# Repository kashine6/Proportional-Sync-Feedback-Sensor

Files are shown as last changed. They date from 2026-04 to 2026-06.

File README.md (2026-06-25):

# PSF (Proportional Sync Feedback) Sensor for MMU

> **A kit made by the author is now available on AliExpress.**
>   
> [Vano3dla-Aliexpress](https://www.aliexpress.com/item/1005010470743517.html)
>
> **Authorized Resellers**
> * [DREMC](https://store.dremc.com.au/en-us/products/vano3dla-psf-sensor-kit-proportional-sync-feedback-sensor-for-mmu) (Australia)
> * [OneTwo3D](https://www.onetwo3d.co.uk/product/psf-proportional-sync-feedback-sensor-for-mmu/) (UK)
> 
> **Additional authorization information:**  
> Trianglelab and BLV are authorized to use the PSF Kit in their MMU kits.
>
> Contact me on Discord (Happy Hare): jacksky007  

This is a Mini Proportional Sync Feedback Sensor solution designed for MMU systems.  

**Note:**

1. After updating to V1.1,   
it should be possible to find a usable ADC interface and a suitable voltage interface on **all MMU boards**.
2. Currently shifted to the default **single-spring version**. It provides constant compression, which reduces the apparent load on the extruder stepper and helps overcome Bowden friction.
   The STLs folder still includes the dual-spring version, which has already been deprecated.
3. **HappyHare** provides strong support for PSF. [WIKI LINK](https://github.com/moggieuk/Happy-Hare/wiki/Synchronized-Gear-Extruder)  
Now HappyHare supports using the PSF as the extruder entry sensor for filament detection.[PULL](https://github.com/moggieuk/Happy-Hare/pull/936)
4. **AFC** currently does not support PSF.
5. This is a prototype design. You can use the PCB below to develop your own custom mods or designs, or even simply use a Hall sensor instead of the PCB.

**Other case versions:**

1. **Ningpj** designed a **More Stumpy version** for ERCF.  [LINK](https://github.com/ningpj/Stumpy_PSF_Sensor)
2. An version developed by **DW-Tas** for **EMU**.  [LINK](https://github.com/DW-Tas/EMU/tree/main/STL/Tension-compression-sensor/Proportional%20Sync%20Feedback%20(PSF)%20Version)
3. An version developed by **Batalhoti** for **quattro-box v2**.  [LINK](https://github.com/Batalhoti/QuattroBox/tree/main/QuattroBox_v2_Beta/STLs/hub_psf)

## 🧩 What Is a Proportional Sync Feedback Sensor?

The Proportional Feedback Sensor is a more advanced feedback solution that uses analog signals.

Unlike other solutions that rely on D2F switches, it:

- **Outputs a signal ranging from 0 to 1**
- **0.5 represents the neutral position**

With this signal, the printer can determine the exact current position of the feedback slider and adjust it toward neutral at any moment.

Happy-Hare has developed many powerful additional features for this type of sensor. 

For details, please refer to the relevant Happy-Hare documentation.

## 🛠 Hardware Design

This design does not use a dedicated standalone mainboard.
Instead, it leverages the ADC input already available on existing MMU boards.

If you want to produce the boards yourself, the **PCB Gerber files** are provided and can be used under the license.
If you prefer not to make the boards yourself, you can get the kit mentioned below.

Both the DRV5055A2 and MT9105ET Hall sensors can be used in my test.

**✅ PSF Board Schematic and PCB**

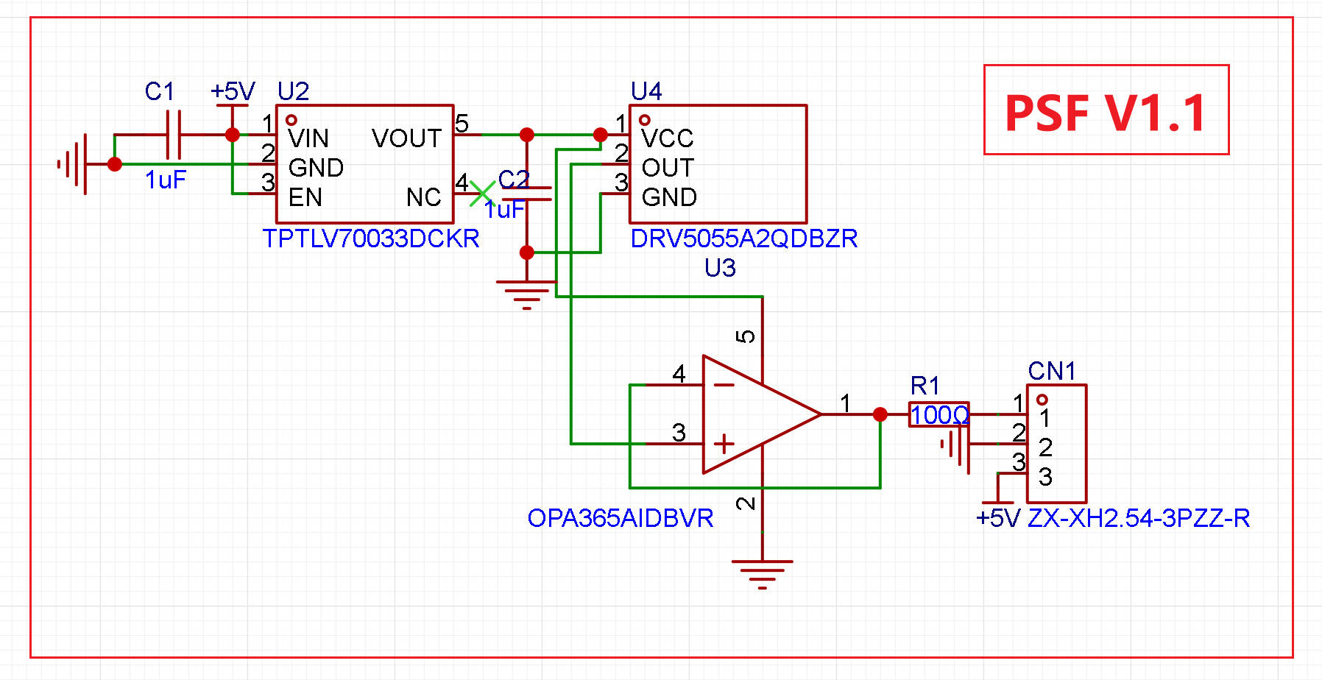
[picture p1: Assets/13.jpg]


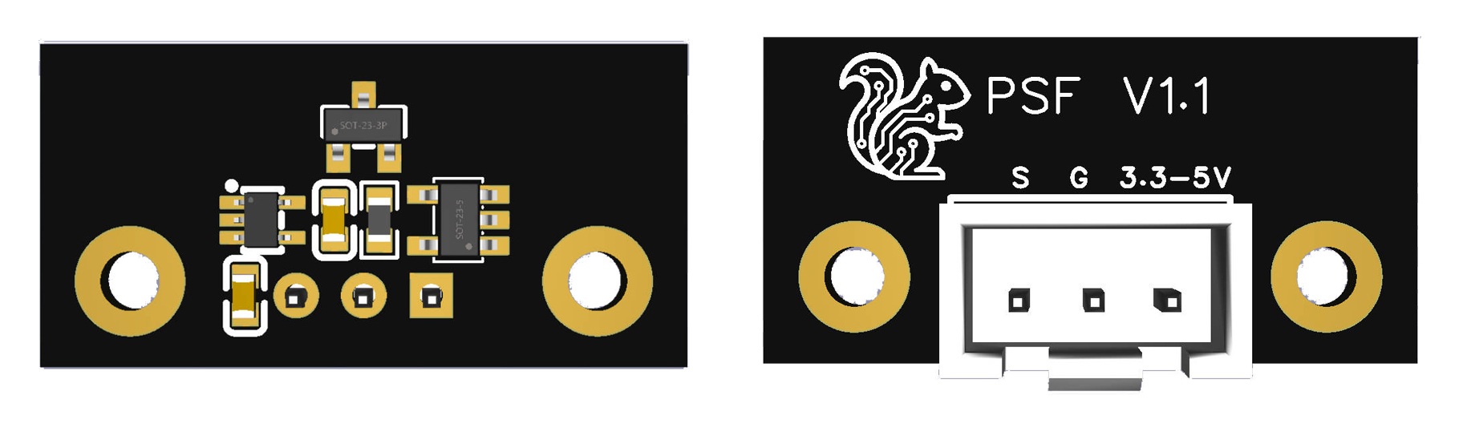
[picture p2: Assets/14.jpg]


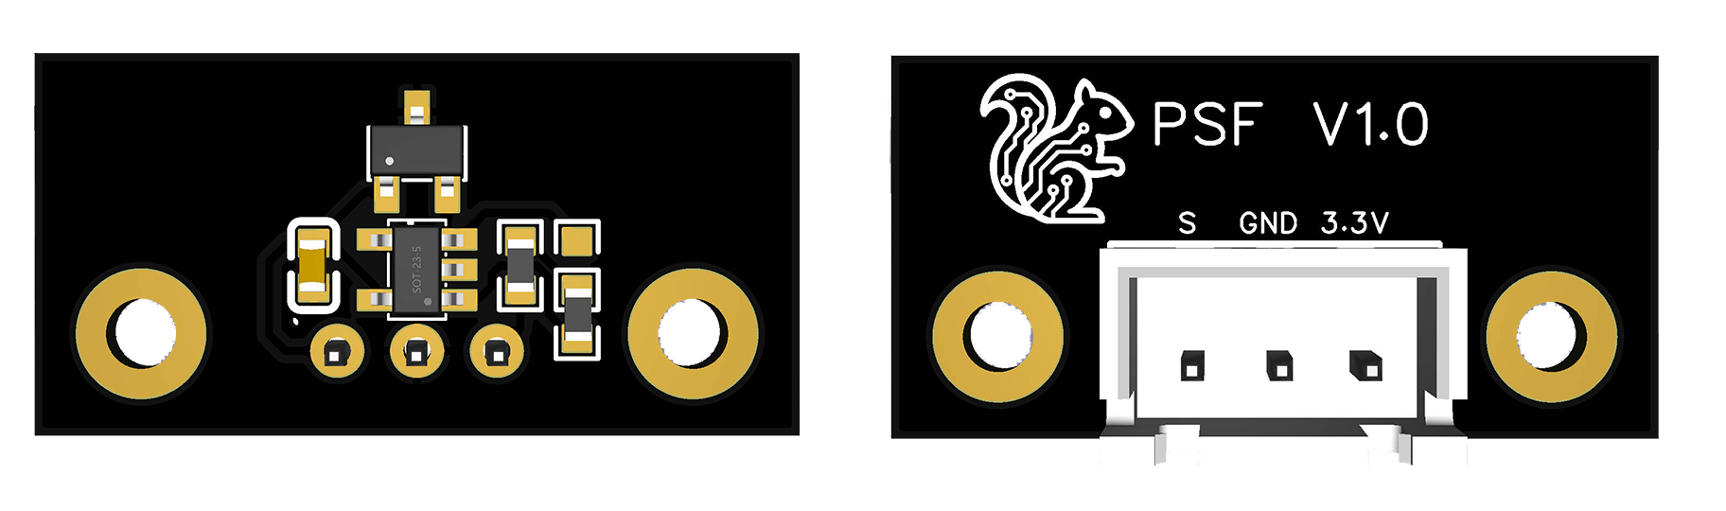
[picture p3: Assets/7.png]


**✅PCB Changelog**

V1.1
- Added wide input voltage support (3.3V–5V) compared to v1.0

V1.0
- Supports 3.3V input only
- Compatible with ADC interfaces with and without pull-up resistors

**✅Important Notice**

- You must connect the signal output to a pin that supports ADC input.

  > Recommended ADC Pins for common mainboards are shown in the diagram below.

- Version 1.1 supports a wide input voltage range of 3.3V–5V, while version 1.0 requires the power input to be 3.3V only.

  > ⚠️⚠️Do NOT use `5V` in Version 1.0 — this may damage your controller board.⚠️⚠️

**✅ADC Pull-up Considerations** 

Some boards—such as **MMB, EBB36, or EBB42**—have **built-in pull-up resistors** on all available ADC inputs.

To support both boards with and without pull-up resistors,  this sensor board uses a special design compatible with both cases.

Using an MMU board with ADC pull-ups will cause the sensor's ADC reading to shift upward (not constant; this has been minimized using the amplifier). 
You can adjust the neutral position value in the configuration to fix this issue.

## 📍 Recommended ADC GPIOs
You can refer to the chip datasheet to find all GPIOs that support ADC. Below, only one usable pin is marked.  

A list of recommended ADC-capable GPIOs for common MMU boards will be provided below:
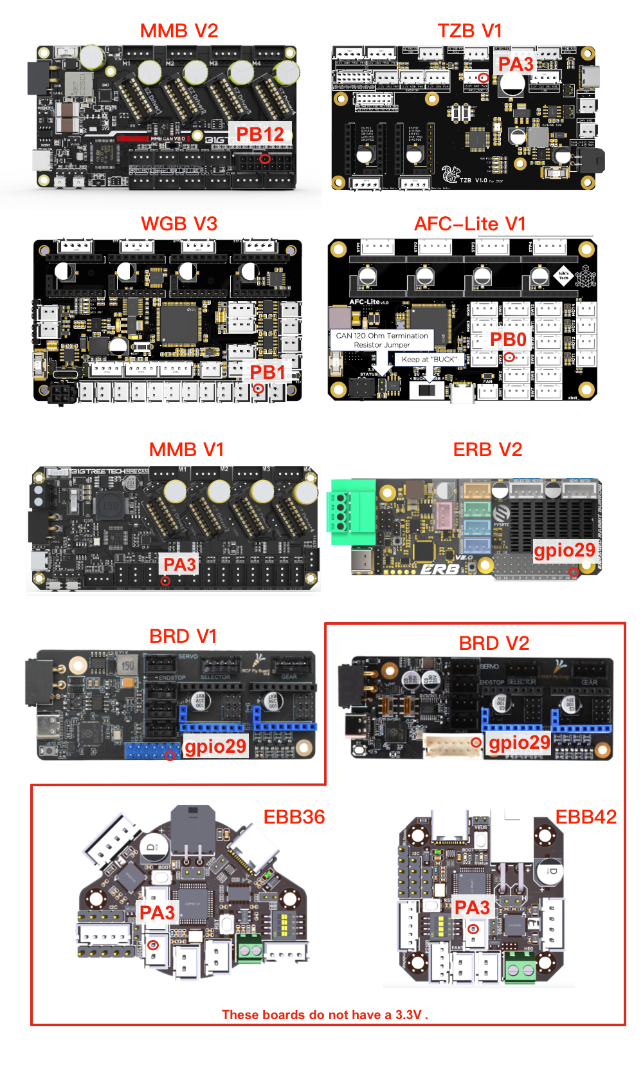
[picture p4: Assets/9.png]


## 📦 Bill of Materials (BOM)

| Item | Specification | Quantity |
| --- | --- | --- |
| **PSF Board** | — | 1 |
| **Spring** | 0.4 mm × 6 mm × 25 mm, spring steel | 1 |
| **Magnet** | D4 mm × 15 mm N35 | 1 |
| **ECAS04 Bowden connector** | — | 2 |
| **ECAS_Clip** | Please use the STL file for printing to ensure consistent thickness | 2 |
| **M2×6 mm SHCS screw** | | 4 |
| **5V-to-3.3V Step-Down Module** | Optional: Only required for V1.0 PCB if your board doesn’t provide a 3.3V. | 1 |

**A kit is available on AliExpress:**  

[Aliexpress](https://www.aliexpress.com/item/1005010470743517.html)

## 🔧 Configuration & Calibration

At the moment, `Happy-Hare` has **integrated** support for Proportional Feedback Sensors, and the relevant Wiki documentation has already been published. 

👉➡️:  [https://github.com/moggieuk/Happy-Hare/wiki/Synchronized-Gear-Extruder](https://github.com/moggieuk/Happy-Hare/wiki/Synchronized-Gear-Extruder) 

For more detailed configuration, please refer to the HappyHare Wiki.

For PSF Sensor one-Spring:  

```  
sync_feedback_buffer_range: 14.5		# Travel in "buffer" between compression/tension or one sensor and end (see above)
sync_feedback_buffer_maxrange: 14.5	    # Absolute maximum end-to-end travel (mm) provided by buffer (see above)  
```

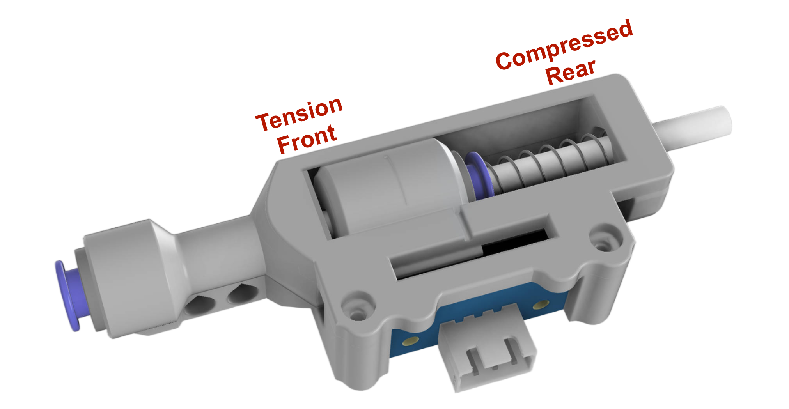
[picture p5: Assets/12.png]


#### ✅ PSF Automatic Calibration

Happy-Hare provides a calibration command, `MMU_CALIBRATE_PSENSOR`, to automatically calibrate the values of the three ADCs. 

Before running this command, you need to load the filament into the toolhead.

**Note:** If the extruder slips or repeated testing at the same position causes abnormal results, you can use manual calibration, which is simpler.

```
$ MMU_CALIBRATE_PSENSOR
...
// Calibration Results:
// As wired the recommended setting (in mmu_hardware.cfg) is:
// [mmu_sensors]
// sync_feedback_analog_max_compression: 0.0023
// sync_feedback_analog_max_tension:     0.9979
// sync_feedback_analog_neutral_point:   0.5001
// After updating, restart klipper
...
```
Please manually update the test results in the hardware.cfg file.

#### ✅ PSF Manual Calibration

Happy-Hare provides a command, `MMU_QUERY_PSENSOR`, to obtain the current raw ADC value. 

```
$ MMU_QUERY_PSENSOR
echo: PSENSOR Enabled: True  Value: -1.0  Raw Value: 0.997
```

You can remove the PSF PCB and place it in a magnetic-field-free environment, use this command to get the value of `sync_feedback_analog_neutral_point`. 

Then, move the slider to the Tension and Compression positions respectively to obtain the values of `sync_feedback_analog_max_tension` and `sync_feedback_analog_max_compression`.



## 🙏 References & Acknowledgements

- The CAD design is based on modifications of [Tshine's Filament Sync Sensor](https://makerworld.com/en/models/507573).  
- The Proportional Sync Feedback concept is inspired by [OpenAMS FPS](https://github.com/OpenAMSOrg/filament-buffer).  
- Thanks to moggieuk, igiannakas, ningpj and KnightRadiant for their excellent code contributions related to Proportional Sync Feedback.

## 😢 License

**This work is licensed under a**
[Creative Commons Attribution-NonCommercial-ShareAlike 4.0 International License][cc-by-nc-sa].

[][cc-by-nc-sa]

[cc-by-nc-sa]: http://creativecommons.org/licenses/by-nc-sa/4.0/
[cc-by-nc-sa-image]: https://licensebuttons.net/l/by-nc-sa/4.0/88x31.png
[cc-by-nc-sa-shield]: https://img.shields.io/badge/License-CC%20BY--NC--SA%204.0-lightgrey.svg

**License clarification regarding use (PCB only):**

- If you are an individual user, feel free to use it. You may choose to purchase a kit or manufacture the PCB yourself using the provided Gerber files.

- If you wish to sell PFS as a product, you must obtain a commercial license beforehand. 

- You may refer to this design for use in other applications, but proper attribution and authorization are required.

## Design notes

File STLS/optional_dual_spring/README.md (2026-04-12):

##  ⚙️ Calibration for dual_spring

**1. Enable detailed logging**

In `mmu_parameters.cfg`, temporarily set:

```
log_level: 4
```

This will let you observe the sensor state in real time.

You need to adjust the configuration in the `mmu_hardware.cfg` file within HappyHare according to the situation.

**2. Determine the correct direction (`sync_feedback_fps_reversed`)**

Move the slider to its left and right limit positions and observe the log output:

- If the front-end trigger reports `tension`, set:

  ```
  sync_feedback_fps_reversed: True
  ```

- If the front-end trigger reports **`compressed`**, set:

  ```
  sync_feedback_fps_reversed: False
  ```

**3. Set the neutral position (`sync_feedback_fps_set_point`)**

```
sync_feedback_fps_set_point: 0.5
```

Notes:

- On boards `without ADC pull-ups`, the idle value should be very close to **0.5**.
- On boards `with pull-ups`, a small offset is normal (typically **0.45–0.55**).
- You may adjust this value slightly depending on whether the neutral reading drifts toward 0 or toward the extremes.
- Whether the value rises or falls depends on the `magnet orientation.

**4. Adjust the usable range (`sync_feedback_fps_range_multiplier`)**

The Hall sensor is non-linear near its extremes, so the design does not use the full ADC range by default.

Increase this multiplier (e.g., **1.1 or 1.2**) so that the left/right extremes map closer to ±1 in the firmware logs.

Example log messages when correctly tuned:

```
STEPPER: MmuSyncFeedbackManager(inactive): Got sync force feedback update. State: tension (-1.0)
STEPPER: MmuSyncFeedbackManager(inactive): Got sync force feedback update. State: compressed (1.0)
```

Default value:

```
sync_feedback_fps_range_multiplier: 1.0
```

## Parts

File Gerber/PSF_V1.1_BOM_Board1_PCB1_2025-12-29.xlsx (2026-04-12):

No. | Quantity | Comment | Designator | Footprint | Value | Manufacturer Part | Manufacturer | Supplier Part | Supplier
1 | 2 | 1uF | C1,C2 | C0603 | 1uF | CGA0603X5R105K500JT | HRE(芯声) | C6119852 | LCSC
2 | 1 | 100Ω | R1 | R0603 | 100Ω | RC0603FR-07100RL | YAGEO(国巨) | C105588 | LCSC
3 | 1 | ZX-XH2.54-3PZZ-R | S G | CONN-TH_3P-P2.50_ZX-XH2.54-3PZZ-R |  | ZX-XH2.54-3PZZ-R | Megastar(兆星) | C22388625 | LCSC
4 | 1 | TPTLV70033DCKR | U2 | SC-70-5_L2.1-W1.3-P0.65-LS2.2-BR |  | TPTLV70033DCKR | TECH PUBLIC(台舟) | C3021117 | LCSC
5 | 1 | OPA365AIDBVR | U3 | SOT-23-5_L3.0-W1.7-P0.95-LS2.8-BR |  | OPA365AIDBVR | TI(德州仪器) | C96626 | LCSC
6 | 1 | DRV5055A2QDBZR | U4 | SOT-23_L2.9-W1.3-P1.90-LS2.4-BR |  | DRV5055A2QDBZR | TI(德州仪器) | C266131 | LCSC

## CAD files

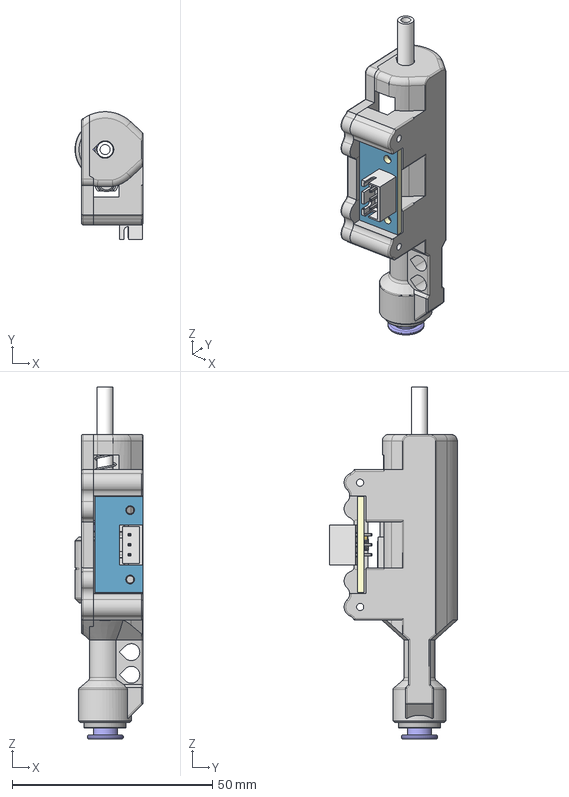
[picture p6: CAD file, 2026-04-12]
CAD/PFS-assembly-one-spring.step
16.9 x 31.8 x 87.8 mm
sensor_housing
sensor_housing_1
slider
Magnet_D4x15
MAuh-Board
MAuh-U1-SOT-23-3_L2.9-W1.6-P1.90-LS2.8-BR-CW
MAuh-C1-C0603
ECAS Fitting v1 x 2
PTFE
Spring_0.4x5x25

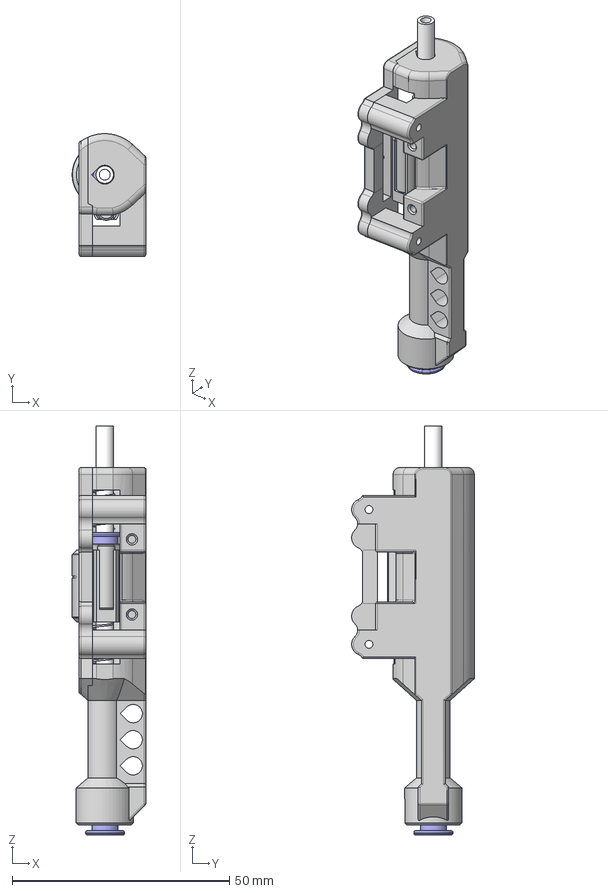
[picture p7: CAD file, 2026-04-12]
CAD/PFS-assembly-dual-spring.step
16.9 x 28.2 x 94.1 mm
sensor_housing
sensor_housing_1
slider
Magnet_D4x15
ECAS Fitting v1 x 2
Spring_0.4x5x25 x 2
PTFE

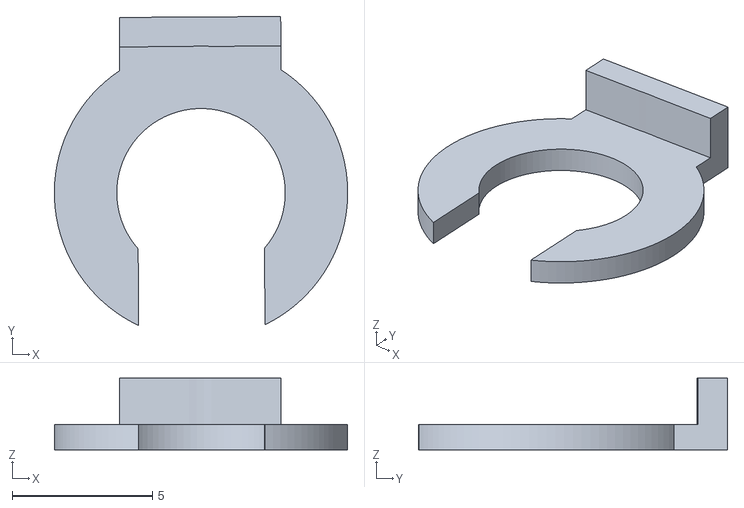
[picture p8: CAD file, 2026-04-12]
STLS/ECAS_Clip_x2.stl
10.4 x 11.0 x 2.56

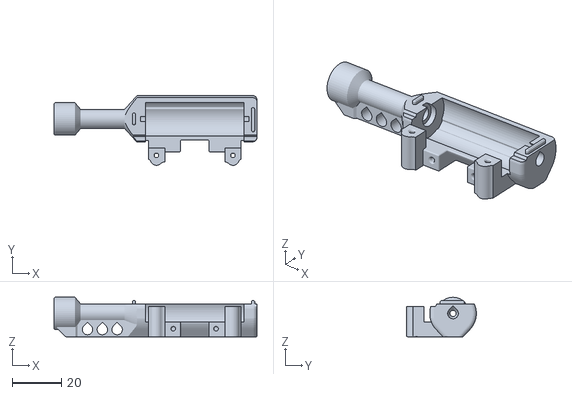
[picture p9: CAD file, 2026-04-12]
STLS/optional_dual_spring/sensor_housing.stl
82.2 x 28.2 x 16.0

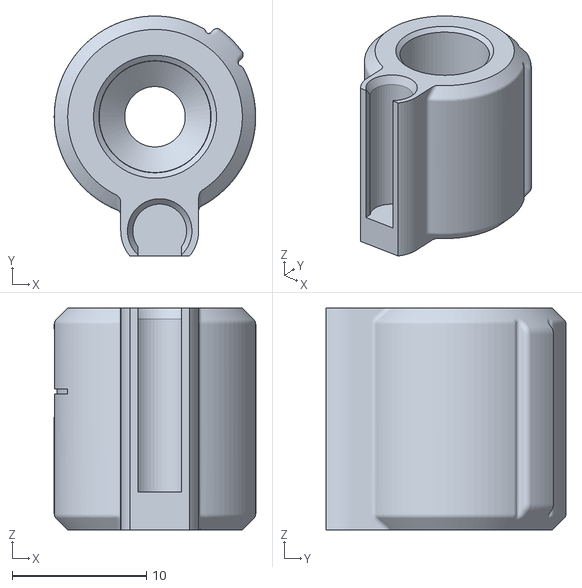
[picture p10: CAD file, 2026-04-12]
STLS/optional_dual_spring/slider.stl
15.0 x 17.9 x 16.5

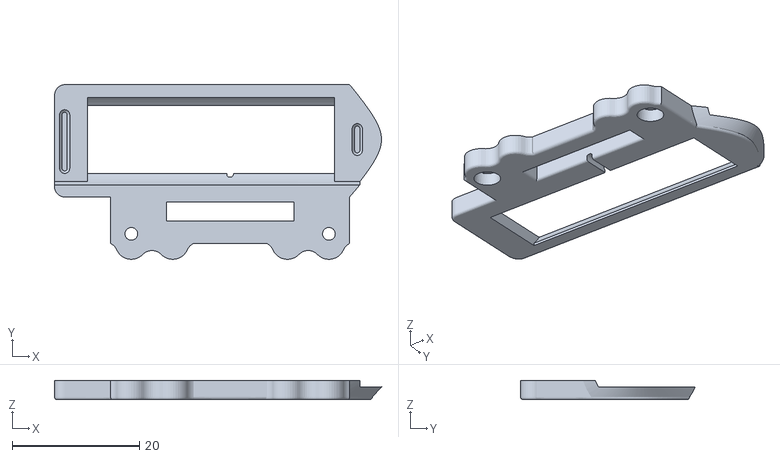
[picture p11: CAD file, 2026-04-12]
STLS/buffer_cover.stl
51.3 x 27.4 x 3.04

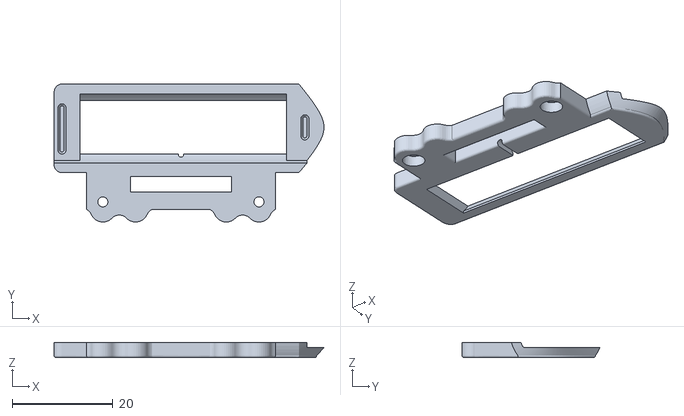
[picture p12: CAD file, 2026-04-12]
STLS/optional_dual_spring/buffer_cover.stl
53.6 x 27.4 x 3.04

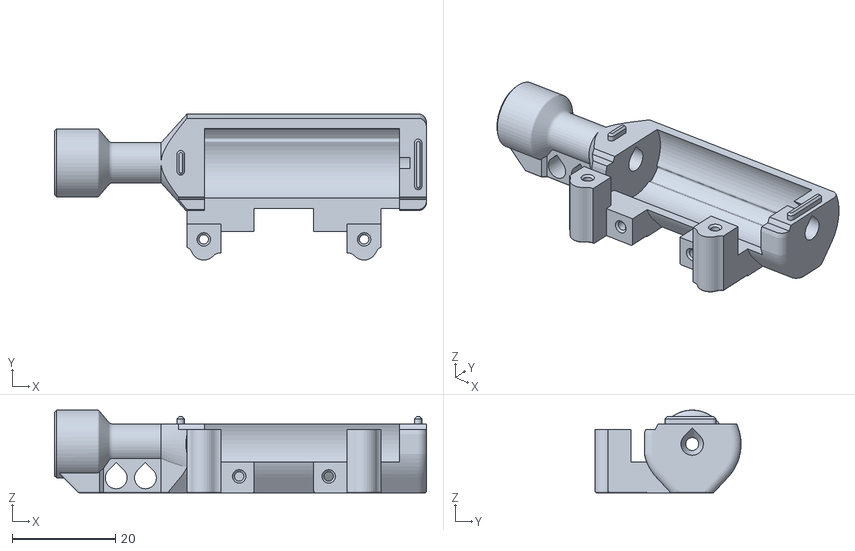
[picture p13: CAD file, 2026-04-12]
STLS/sensor_housing.stl
71.9 x 28.2 x 16.0

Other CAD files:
STLS/slider.stl
